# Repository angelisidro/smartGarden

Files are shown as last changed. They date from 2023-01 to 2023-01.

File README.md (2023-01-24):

# Smart Garden

## Instalación de la Tarjeta de control Smart Garden

Para la instalación en Arduino IDE debemos seguir los siguientes pasos:

1. Abrir ARDUINO IDE
2. Debemos ir a la pestaña ***Archivo***->***Preferencias***.
	- En la pestaña ***Ajustes*** buscamos la opción: ***Gestor de URLs Adicionales de Tarjetas: ***
	- Pegamos la siguiente URL: `https://dl.espressif.com/dl/package_esp32_index.json`
	- Luego presionamos la opción ***OK*** y automáticamente se cerrará la ventana.
3. Debemos ir a la pestaña ***Herramientas***->***Placa***->***Gestor de tarjetas***.
	- Colocamos en la barra de búsqueda ***ESP32***.
	- Seleccionamos la opción que nos muestre ***ESP32 Wrover Module***.
	- Instalamos y luego presionamos la opción de ***Cerrar***.

Con esto tendremos completa la instalación de nuestra tarjeta ESP32 y lista para ser programada.	 

## Instalación USB Driver ***(Si no reconoce el puerto COM)***

En algunos casos nuestra PC no es capaz de reconocer el dispositivo USB que nosotros conectamos, es por ello que dejaremos un archivo para la instalación del driver con ello nuestra PC deberá ser capaz de reconocer el dispositivo conectado, en caso de que el problema persista asegúrese de que su dispositivo no se este sobre calentando.

[Descarga este driver para Windows][DRIVER_USB]

[DRIVER_USB]: https://www.arduined.eu/files/windows10/CH341SER.zip

1. Descomprimir el archivo ZIP descargado 
2. Seleccionar el archivo para instalación de Windows
	- SETUP.exe
3. Seleccionar CH341SER.INF
4. Click en la opción ***Install***
5. Cuando este instalado cerrar la ventana y listo.!

Con esto estaría lista la instalación del Driver USB para nuestra tarjeta en el Sistema Operativo Windows.

Puede seguir está guía para la instalación como una segunda opción 

[Sigue la guía para instalar el driver CH340][DRIVER_CH340]

[DRIVER_CH340]: https://www.arduined.eu/ch340-windows-10-driver-download/

## Pinout

### Alimentación de la tarjeta de control
Nombre | GPIO 
--- | --- 
VDD | 5V - 9V
VSS | GND

### Bomba de Agua No.1
Nombre | GPIO 
--- | --- 
AIN1 | 32
AIN2 | 33

### Bomba de Agua No.2
Nombre | GPIO 
--- | --- 
BIN1 | 25
BIN2 | 26

### Luz UV (Ultravioleta)
Nombre | GPIO 
--- | --- 
VDD | 5V
VSS | GND

### Higrómetro (Humedad de Suelo)
Nombre | GPIO 
--- | --- 
DATA | 19
VDD | 3V3 - 5V
VSS | GND

### I2C Connector STEMMA

Nombre | GPIO 
--- | --- 
SCL | 22
SDI | 21
VDD | 3V3
VSS | GND

### Prueba de Bomba de Agua

[Visita el código base en el siguiente link][prueba_motore]

[prueba_motore]: https://github.com/teslalab/smartGarden/tree/main/ejemplos%20smart%20garden%20-%20balam%202022/balam2022-prueba-motores-v1

### Prueba de Sensor Humedad de Suelo

[Visita el código base en el siguiente link][prueba_higro]

[prueba_higro]: https://github.com/teslalab/smartGarden/tree/main/ejemplos%20smart%20garden%20-%20balam%202022/22020601-balam2022-sensor_humedad_suelo-test

### Prueba de Sensor UV

[Visita el código base en el siguiente link][prueba_UV]

[prueba_UV]: https://github.com/teslalab/smartGarden/tree/main/ejemplos%20smart%20garden%20-%20balam%202022/20220601-balam2022-sensorSI1133

### Prueba de Sensor Humedad y Temperatura Ambiente BME688

[Visita el código base en el siguiente link][cotrol_BME688]

[control_BME688]: https://github.com/teslalab/smartGarden/tree/main/ejemplos%20smart%20garden%20-%20balam%202022/20220601-balam2022-sensorBME

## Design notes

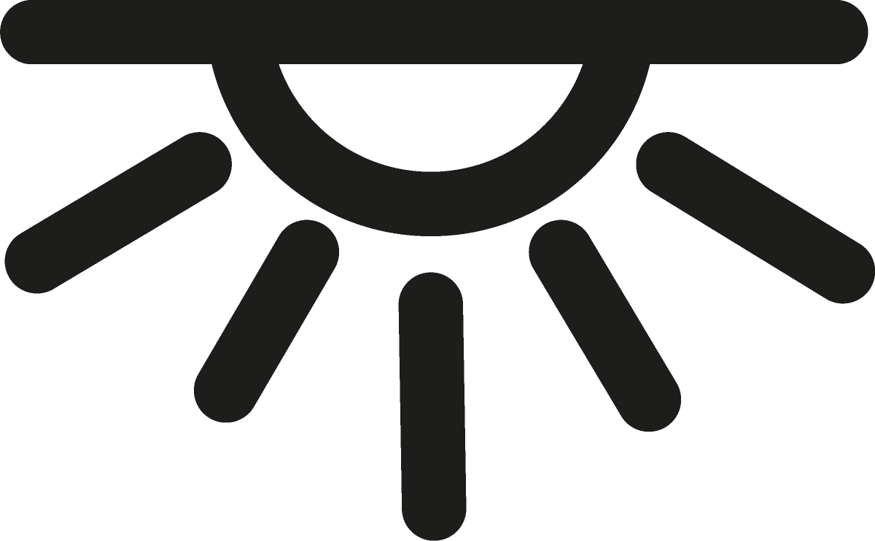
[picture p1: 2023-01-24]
PCB_Smart_Garden/UV.bmp

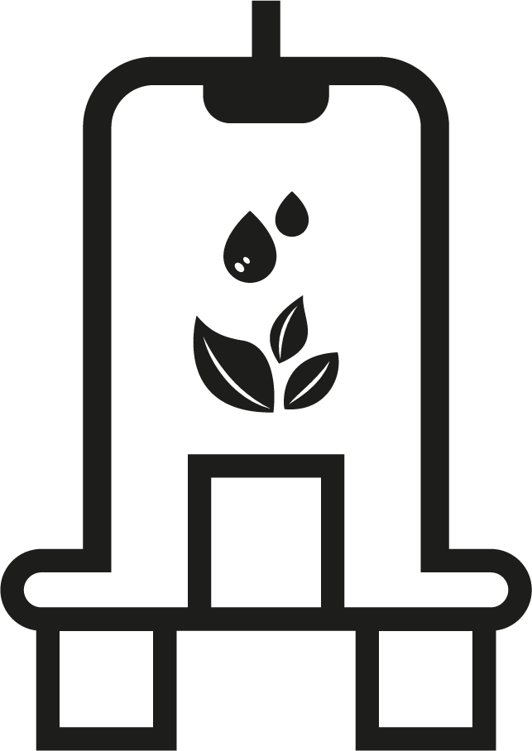
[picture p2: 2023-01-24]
PCB_Smart_Garden/SILK.bmp

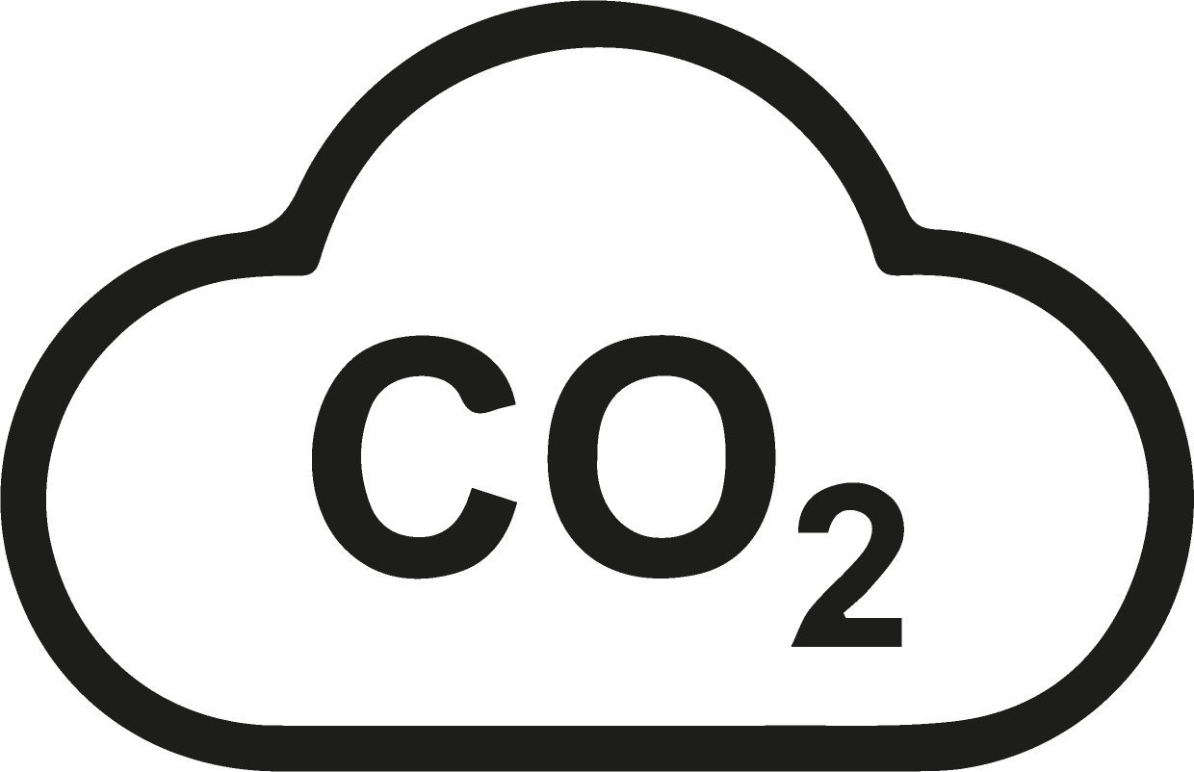
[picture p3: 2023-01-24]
PCB_Smart_Garden/CO2.bmp

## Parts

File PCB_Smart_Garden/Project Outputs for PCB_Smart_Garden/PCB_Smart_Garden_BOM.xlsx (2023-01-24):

Comment | Description | Designator | Footprint | LibRef | Quantity | Total
0805ZD225KAT2A | Chip Capacitor, 2.2 uF, +/- 10%, 10 V, -55 to 85 degC, 0805 (2012 Metric), RoHS, Tape and Reel | C1 | CAPC2013X140X50ML20T25 | CMP-2000-05810-1 | 1 | 50
0.1 uF | Chip Capacitor, Ceramic, 0.1 uF, 10%, 50 V, 0805, RoHS, Tape and Reel | C2 | CAPC2013X94X50ML20T25 | CMP-2000-05016-1 | 1 | 50
Comment |  | Designator12 | 61300611121 |  | 1 | 50
PH1-19-UA | Connector Header Through Hole 19 position 0.100" (2.54mm) | J1, J2 | PH1-19-UA - SOCKET | PH1-19-UA | 2 | 100
SM04B-SRSS-TB(LF)(SN) | Connector Header Surface Mount, Right Angle 4 position 0.039 _1.00mm_ | J3, J4 | JST_SM04B-SRSS-TB(LF)(SN) | SM04B-SRSS-TB(LF)(SN) | 2 | 100
282836-2 | Female Header, Pitch 5 mm, 1 x 2 Position, Height 10 mm, Tail Length 3.5 mm, Rohs, Bulk | J5 | TECO-282836-2_V | CMP-1684-00017-1 | 1 | 50
691214110002 | Serie 2141 - 3.50 mm Horizontal Entry Modular with Rising Cage Clamp WR-TBL, 2 pin | MOTOR_1, MOTOR_2, V_EXT1 | 691214110002 | CMP-1502-02464-1 | 3 | 150
EG1218 | Slide Switch, 500 V, -20 to 70 degC, 3-Pin THD, RoHS | ON/OFF | ESWI-EG1218_V | CMP-1696-00002-1 | 1 | 50
61300411121 | THT Vertical Pin Header WR-PHD, Pitch 2.54 mm, Single Row, 4 pins | P1 | 61300411121 | CMP-1502-01064-1 | 1 | 50
TSW-103-07-F-S | 0.025" SQ Post Header, Through-hole, Vertical, -55 to 125 degC, 2.54 mm Pitch, 3-Pin, Male, RoHS | P2 | SMTC-TSW-103-07-X-S | CMP-1024-00331-1 | 1 | 50
ERA6AEB473V |  | R1 | RESC2013X60X40ML20T25 | CMP-2001-00645-1 | 1 | 50
DRV8833PW | 2 A Low Voltage Dual Brushed DC or Single Bipolar Stepper Motor Driver (PWM Ctrl), 2.7 to 10.8 V, -40 to 85 degC, 16-Pin SOP (PW), Green (RoHS & no Sb/Br), Tube | U1 | PW0016A_M | CMP-1529-00002-2 | 1 | 50

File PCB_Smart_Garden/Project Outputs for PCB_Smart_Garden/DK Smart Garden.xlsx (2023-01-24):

Index | Quantity | Part Number | Manufacturer Part Number | Description | Customer Reference | Available | Backorder | Unit Price | Extended Price USD
1 | 100 | 2057-PH1-19-UA-ND | PH1-19-UA | CONN HEADER VERT 19POS 2.54MM |  | 100 | 0 | 0.2037 | 20.37
2 | 150 | 732-2747-ND | 691214110002 | TERM BLK 2POS SIDE ENT 3.5MM PCB |  | 150 | 0 | 0.591 | 88.65
3 | 50 | EG1903-ND | EG1218 | SWITCH SLIDE SPDT 200MA 30V |  | 50 | 0 | 0.6996 | 34.98
4 | 50 | 732-5317-ND | 61300411121 | CONN HEADER VERT 4POS 2.54MM |  | 50 | 0 | 0.11 | 5.50
5 | 50 | SAM8995-ND | TSW-103-07-F-S | CONN HEADER VERT 3POS 2.54MM |  | 50 | 0 | 0.381 | 19.05
6 | 50 | 478-1413-1-ND | 0805ZD225KAT2A | CAP CER 2.2UF 10V X5R 0805 |  | 50 | 0 | 0.1162 | 5.81
7 | 50 | 478-1413-1-ND | 0805ZD225KAT2A | CAP CER 2.2UF 10V X5R 0805 |  | 50 | 0 | 0.1162 | 5.81
8 | 100 | 455-1804-1-ND | SM04B-SRSS-TB(LF)(SN) | CONN HEADER SMD R/A 4POS 1MM |  | 0 | 100 | 0.4063 | 40.63
9 | 50 | P47KDACT-ND | ERA-6AEB473V | RES 47K OHM 0.1% 1/8W 0805 |  | 50 | 0 | 0.301 | 15.05
10 | 50 | P47KDACT-ND | ERA-6AEB473V | RES 47K OHM 0.1% 1/8W 0805 |  | 50 | 0 | 0.301 | 15.05
11 | 50 | A98076-ND | 282836-2 | TERM BLK 2POS SIDE ENTRY 5MM PCB |  | 0 | 50 | 0.365 | 18.25
12 | 50 | 732-5319-ND | 61300611121 | CONN HEADER VERT 6POS 2.54MM |  | 50 | 0 | 0.201 | 10.05

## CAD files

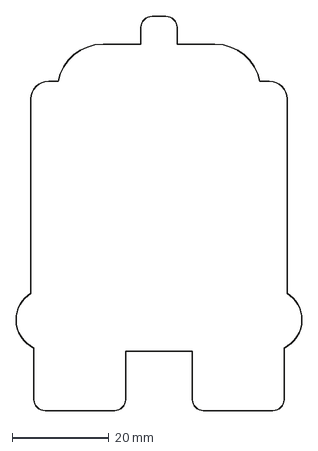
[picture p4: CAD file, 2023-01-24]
PCB_Smart_Garden/EDGE.dxf
58.9 x 81.3 mm
